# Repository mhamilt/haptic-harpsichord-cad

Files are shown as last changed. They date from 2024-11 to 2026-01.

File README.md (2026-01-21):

# Haptic Harpsichord CAD
Repository of CAD project files for the [Haptic Harpsichord](https://github.com/mhamilt/harpsichord-jack-tracking)

## Components

### QRE1113

- [QRE1113 Datasheet](https://www.mouser.in/datasheet/2/308/QRE1113-1121523.pdf)

|  |  |
| :---: | :---: |
| QRE1113 Dimension. Not that pin 1 should always have a chamfer on the corner to help identify it. | QRE1113 Pinout |

### Multiplexer

- Datasheet

### LEDs

- Datasheet

### Rotary

- Datasheet

### FRAM

- Datasheet

## Eagle 

### Automating EAGLE Commands

Below is python code used to generate commands that can be copy and pasted into EAGLE.

EAGLE has it's [ULP](https://web.mit.edu/xavid/arch/i386_rhel4/help/129.htm), but the intention here is to provide a light weight and easily modifiable system.

#### Faceboard

```py
qrepitch = 1.8 # placement is calculated from the #1 pin, pitch is used to offset to the centre
ox = 1.705     # min distance from board edge
oy = 1.705     # min distance from board edge in y axis
pitch = 14.02 # jack pitch
max_board_width = (6*pitch) + ox + qrepitch + ox

for index, point in enumerate([(x * pitch) + ox for x in range(0,7)]):
  print(f"move Q{index+1} ({oy} {point});")

resitor100k_ox = 10.1 # min distance from board edge in y axis
resitor100k_oy = 7.0 # min distance from board edge in y axis
resitor100_ox = 7.5 # min distance from board edge in y axis
resitor100_oy = 7.0 # min distance from board edge in y axis
rpitch = 12.9

for index, point in enumerate([(x * rpitch) + resitor100_oy for x in range(0,16)]):
  if index < 7:
    print(f"move R{(index*2)+1} ({resitor100_ox} {point});")
    print(f"move R{(index+1)*2} ({resitor10k_ox} {point});")
  if index >= 7:
    print(f"move R{((index+1)*2)+1} ({resitor100_ox} {point});")
    print(f"move R{((index+1)+1)*2} ({resitor10k_ox} {point});")

led_ox = 23.08 # min distance from board edge in x axis
led_ox = 23.68
# led_oy = 4.4 # min distance from board edge in y axis
# led_pitch = 12.0
led_pitch = 17.73 - 3.71
led_oy = 3.71 + (qrepitch/2) # min distance from board edge in y axis

for index, point in enumerate([(x * led_pitch) + led_oy for x in range(0,7)]):
  print(f"rotate D{(index+1)} 270;")
  print(f"move D{(7-index)} ({led_ox} {point});")
  print(f"mirror D{(index+1)};")

```

#### Sensor Board

```py
ox = 1.705         # mm min distance from board edge
oy = 1.705         # mm min distance from board edge in y axis
rotx = 3.55        # mm min x distance but for a 90 rotated sensor
jack_pitch = 14.02 # mm

led_ox = 23.08 # min distance from board edge in x axis
led_pitch = 17.73 - 3.71 # mini 3535 neopixels

for i, p in enumerate([(x * jack_pitch) + oy for x in range(0,7)]):
  print(f"ROTATE =R90 Q{i+1};")

for i, p in enumerate([(x * jack_pitch) + oy for x in range(0,7)]):
  print(f"move Q{i+1} ({rotx} {p});")

for i, p in enumerate([(x * led_pitch) + led_oy for x in range(0,7)]):
  print(f"ROTATE =R90 LED{i+1};")

for index, point in enumerate([(x * led_pitch) + led_oy for x in range(0,7)]):  
  print(f"move LED{(index+1)} ({led_ox} {point});")

for index, point in enumerate([(x * led_pitch) + led_oy for x in range(0,7)]):  
  print(f"mirror LED{(index+1)};")

```

#### Sensor Board SMD

```py
ox = 1.705         # mm min distance from board edge
oy = 1.705         # mm min distance from board edge in y axis
rotx = 3.55        # mm min x distance but for a 90 rotated sensor
jack_pitch = 14.02 # mm

led_ox = 23.08 # min distance from board edge in x axis
led_pitch = 17.73 - 3.71 # mini 3535 neopixels

for i, p in enumerate([(x * jack_pitch) + oy for x in range(0,7)]):
  print(f"ROTATE =R90 Q{i+1};")

for i, point in enumerate([(x * jack_pitch) + ox for x in range(0,7)]):
  print(f"move Q{i+1} ({oy} {p});")

for i, p in enumerate([(x * led_pitch) + led_oy for x in range(0,7)]):
  print(f"ROTATE =R90 LED{i+1};")

for i, p in enumerate([(x * led_pitch) + led_oy for x in range(0,7)]):  
  print(f"move LED{(i+1)} ({led_ox} {point});")

for i, p in enumerate([(x * led_pitch) + led_oy for x in range(0,7)]):  
  print(f"mirror LED{(i+1)};")

```

## Mount Holes

### Sensor Board

```
Mount Holes: (4.5 81.5), (4.5 11) 
```
### Signal Board

```
Mount Holes: (12.5 75), (12.5 18) 
```

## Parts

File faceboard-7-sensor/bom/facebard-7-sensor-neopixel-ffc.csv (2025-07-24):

Part | Value | Device | Package | Description | ARROW_PART_NUMBER | ARROW_PRICE-STOCK | COPYRIGHT | DESCRIPTION | HEIGHT | MANUFACTURER | MANUFACTURER_NAME | MANUFACTURER_PART_NUMBER | MAXIMUM_PACKAGE_HEIGHT | MFR_NAME | MOUSER_PART_NUMBER | MOUSER_PRICE-STOCK | PARTREV | POPULARITY | SPICEPREFIX | STANDARD
D1 | 1655 | 1655 | LED_1655 | Ws2812b 5050 Rgb Led With Integrated Driver Chip Pack Of 10 |  |  |  |  |  | Adafruit Industries |  |  | 1.6 mm |  |  |  | 01 |  |  | Manufacturer recommendations
D2 | 1655 | 1655 | LED_1655 | Ws2812b 5050 Rgb Led With Integrated Driver Chip Pack Of 10 |  |  |  |  |  | Adafruit Industries |  |  | 1.6 mm |  |  |  | 01 |  |  | Manufacturer recommendations
D3 | 1655 | 1655 | LED_1655 | Ws2812b 5050 Rgb Led With Integrated Driver Chip Pack Of 10 |  |  |  |  |  | Adafruit Industries |  |  | 1.6 mm |  |  |  | 01 |  |  | Manufacturer recommendations
D4 | 1655 | 1655 | LED_1655 | Ws2812b 5050 Rgb Led With Integrated Driver Chip Pack Of 10 |  |  |  |  |  | Adafruit Industries |  |  | 1.6 mm |  |  |  | 01 |  |  | Manufacturer recommendations
D5 | 1655 | 1655 | LED_1655 | Ws2812b 5050 Rgb Led With Integrated Driver Chip Pack Of 10 |  |  |  |  |  | Adafruit Industries |  |  | 1.6 mm |  |  |  | 01 |  |  | Manufacturer recommendations
D6 | 1655 | 1655 | LED_1655 | Ws2812b 5050 Rgb Led With Integrated Driver Chip Pack Of 10 |  |  |  |  |  | Adafruit Industries |  |  | 1.6 mm |  |  |  | 01 |  |  | Manufacturer recommendations
D7 | 1655 | 1655 | LED_1655 | Ws2812b 5050 Rgb Led With Integrated Driver Chip Pack Of 10 |  |  |  |  |  | Adafruit Industries |  |  | 1.6 mm |  |  |  | 01 |  |  | Manufacturer recommendations
FFCIN | 52806-1410 | 52806-1410 | 528061410 | Molex 2mm Pitch 14 Way Straight Female FPC Connector |  |  |  | Molex 2mm Pitch 14 Way Straight Female FPC Connector | 5.6mm |  | Molex | 52806-1410 |  |  | 538-52806-1410 | https://www.mouser.co.uk/ProductDetail/Molex/52806-1410?qs=%252BdbFUiYBkDYU5moeZz2crA%3D%3D
FFCOUT | 52806-1410 | 52806-1410 | 528061410 | Molex 2mm Pitch 14 Way Straight Female FPC Connector |  |  |  | Molex 2mm Pitch 14 Way Straight Female FPC Connector | 5.6mm |  | Molex | 52806-1410 |  |  | 538-52806-1410 | https://www.mouser.co.uk/ProductDetail/Molex/52806-1410?qs=%252BdbFUiYBkDYU5moeZz2crA%3D%3D
Q1 | QRE1113 | QRE1113 | DIP4_100AQ_ONS |  |  |  | Copyright (C) 2024 Ultra Librarian. All rights reserved. |  |  |  |  | QRE1113 |  | onsemi
Q2 | QRE1113 | QRE1113 | DIP4_100AQ_ONS |  |  |  | Copyright (C) 2024 Ultra Librarian. All rights reserved. |  |  |  |  | QRE1113 |  | onsemi
Q3 | QRE1113 | QRE1113 | DIP4_100AQ_ONS |  |  |  | Copyright (C) 2024 Ultra Librarian. All rights reserved. |  |  |  |  | QRE1113 |  | onsemi
Q4 | QRE1113 | QRE1113 | DIP4_100AQ_ONS |  |  |  | Copyright (C) 2024 Ultra Librarian. All rights reserved. |  |  |  |  | QRE1113 |  | onsemi
Q5 | QRE1113 | QRE1113 | DIP4_100AQ_ONS |  |  |  | Copyright (C) 2024 Ultra Librarian. All rights reserved. |  |  |  |  | QRE1113 |  | onsemi
Q6 | QRE1113 | QRE1113 | DIP4_100AQ_ONS |  |  |  | Copyright (C) 2024 Ultra Librarian. All rights reserved. |  |  |  |  | QRE1113 |  | onsemi
Q7 | QRE1113 | QRE1113 | DIP4_100AQ_ONS |  |  |  | Copyright (C) 2024 Ultra Librarian. All rights reserved. |  |  |  |  | QRE1113 |  | onsemi
R1 | 100 | R-EU_0207/10 | 0207/10 | RESISTOR, European symbol |  |  |  |  |  |  |  |  |  |  |  |  |  | 81 | R
R3 | 100 | R-EU_0207/10 | 0207/10 | RESISTOR, European symbol |  |  |  |  |  |  |  |  |  |  |  |  |  | 81 | R
R5 | 100 | R-EU_0207/10 | 0207/10 | RESISTOR, European symbol |  |  |  |  |  |  |  |  |  |  |  |  |  | 81 | R
R7 | 100 | R-EU_0207/10 | 0207/10 | RESISTOR, European symbol |  |  |  |  |  |  |  |  |  |  |  |  |  | 81 | R
R9 | 100 | R-EU_0207/10 | 0207/10 | RESISTOR, European symbol |  |  |  |  |  |  |  |  |  |  |  |  |  | 81 | R
R11 | 100 | R-EU_0207/10 | 0207/10 | RESISTOR, European symbol |  |  |  |  |  |  |  |  |  |  |  |  |  | 81 | R
R13 | 100 | R-EU_0207/10 | 0207/10 | RESISTOR, European symbol |  |  |  |  |  |  |  |  |  |  |  |  |  | 81 | R
RDV | 100k | R-EU_0207/10 | 0207/10 | RESISTOR, European symbol |  |  |  |  |  |  |  |  |  |  |  |  |  | 81 | R
SJ1 |  | SJ | SJ | SMD solder JUMPER |  |  |  |  |  |  |  |  |  |  |  |  |  | 33
SJ2 |  | SJ | SJ | SMD solder JUMPER |  |  |  |  |  |  |  |  |  |  |  |  |  | 33
SJ3 |  | SJ | SJ | SMD solder JUMPER |  |  |  |  |  |  |  |  |  |  |  |  |  | 33
SJ4 |  | SJ | SJ | SMD solder JUMPER |  |  |  |  |  |  |  |  |  |  |  |  |  | 33
SJ5 |  | SJ | SJ | SMD solder JUMPER |  |  |  |  |  |  |  |  |  |  |  |  |  | 33
SJ6 |  | SJ | SJ | SMD solder JUMPER |  |  |  |  |  |  |  |  |  |  |  |  |  | 33
SJ7 |  | SJ | SJ | SMD solder JUMPER |  |  |  |  |  |  |  |  |  |  |  |  |  | 33
U1 | CD4051BE | CD4051BE | N16 |  |  |  | Copyright (C) 2024 Ultra Librarian. All rights reserved. |  |  |  |  | CD4051BE |  | Texas Instruments

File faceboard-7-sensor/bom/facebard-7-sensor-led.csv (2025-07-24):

Part | Value | Device | Package | Description | COPYRIGHT | MANUFACTURER | MANUFACTURER_PART_NUMBER | MAXIMUM_PACKAGE_HEIGHT | MF | MFR_NAME | MPN | OC_FARNELL | OC_NEWARK | PARTREV | POPULARITY | SPICEPREFIX | STANDARD
D1 | 1655 | 1655 | LED_1655 | Ws2812b 5050 Rgb Led With Integrated Driver Chip Pack Of 10 |  | Adafruit Industries |  | 1.6 mm |  |  |  |  |  | 01 |  |  | Manufacturer recommendations
D2 | 1655 | 1655 | LED_1655 | Ws2812b 5050 Rgb Led With Integrated Driver Chip Pack Of 10 |  | Adafruit Industries |  | 1.6 mm |  |  |  |  |  | 01 |  |  | Manufacturer recommendations
D3 | 1655 | 1655 | LED_1655 | Ws2812b 5050 Rgb Led With Integrated Driver Chip Pack Of 10 |  | Adafruit Industries |  | 1.6 mm |  |  |  |  |  | 01 |  |  | Manufacturer recommendations
D4 | 1655 | 1655 | LED_1655 | Ws2812b 5050 Rgb Led With Integrated Driver Chip Pack Of 10 |  | Adafruit Industries |  | 1.6 mm |  |  |  |  |  | 01 |  |  | Manufacturer recommendations
D5 | 1655 | 1655 | LED_1655 | Ws2812b 5050 Rgb Led With Integrated Driver Chip Pack Of 10 |  | Adafruit Industries |  | 1.6 mm |  |  |  |  |  | 01 |  |  | Manufacturer recommendations
D6 | 1655 | 1655 | LED_1655 | Ws2812b 5050 Rgb Led With Integrated Driver Chip Pack Of 10 |  | Adafruit Industries |  | 1.6 mm |  |  |  |  |  | 01 |  |  | Manufacturer recommendations
D7 | 1655 | 1655 | LED_1655 | Ws2812b 5050 Rgb Led With Integrated Driver Chip Pack Of 10 |  | Adafruit Industries |  | 1.6 mm |  |  |  |  |  | 01 |  |  | Manufacturer recommendations
Q1 | QRE1113 | QRE1113 | DIP4_100AQ_ONS |  | Copyright (C) 2024 Ultra Librarian. All rights reserved. |  | QRE1113 |  |  | onsemi
Q2 | QRE1113 | QRE1113 | DIP4_100AQ_ONS |  | Copyright (C) 2024 Ultra Librarian. All rights reserved. |  | QRE1113 |  |  | onsemi
Q3 | QRE1113 | QRE1113 | DIP4_100AQ_ONS |  | Copyright (C) 2024 Ultra Librarian. All rights reserved. |  | QRE1113 |  |  | onsemi
Q4 | QRE1113 | QRE1113 | DIP4_100AQ_ONS |  | Copyright (C) 2024 Ultra Librarian. All rights reserved. |  | QRE1113 |  |  | onsemi
Q5 | QRE1113 | QRE1113 | DIP4_100AQ_ONS |  | Copyright (C) 2024 Ultra Librarian. All rights reserved. |  | QRE1113 |  |  | onsemi
Q6 | QRE1113 | QRE1113 | DIP4_100AQ_ONS |  | Copyright (C) 2024 Ultra Librarian. All rights reserved. |  | QRE1113 |  |  | onsemi
Q7 | QRE1113 | QRE1113 | DIP4_100AQ_ONS |  | Copyright (C) 2024 Ultra Librarian. All rights reserved. |  | QRE1113 |  |  | onsemi
R1 | 100 | R-EU_0207/10 | 0207/10 | RESISTOR, European symbol |  |  |  |  |  |  |  |  |  |  | 81 | R
R2 | 100k | R-EU_0207/10 | 0207/10 | RESISTOR, European symbol |  |  |  |  |  |  |  |  |  |  | 81 | R
R3 | 100 | R-EU_0207/10 | 0207/10 | RESISTOR, European symbol |  |  |  |  |  |  |  |  |  |  | 81 | R
R4 | 100k | R-EU_0207/10 | 0207/10 | RESISTOR, European symbol |  |  |  |  |  |  |  |  |  |  | 81 | R
R5 | 100 | R-EU_0207/10 | 0207/10 | RESISTOR, European symbol |  |  |  |  |  |  |  |  |  |  | 81 | R
R6 | 100k | R-EU_0207/10 | 0207/10 | RESISTOR, European symbol |  |  |  |  |  |  |  |  |  |  | 81 | R
R7 | 100 | R-EU_0207/10 | 0207/10 | RESISTOR, European symbol |  |  |  |  |  |  |  |  |  |  | 81 | R
R8 | 100k | R-EU_0207/10 | 0207/10 | RESISTOR, European symbol |  |  |  |  |  |  |  |  |  |  | 81 | R
R9 | 100 | R-EU_0207/10 | 0207/10 | RESISTOR, European symbol |  |  |  |  |  |  |  |  |  |  | 81 | R
R10 | 10k | R-EU_0207/10 | 0207/10 | RESISTOR, European symbol |  |  |  |  |  |  |  |  |  |  | 81 | R
R11 | 100 | R-EU_0207/10 | 0207/10 | RESISTOR, European symbol |  |  |  |  |  |  |  |  |  |  | 81 | R
R12 | 100k | R-EU_0207/10 | 0207/10 | RESISTOR, European symbol |  |  |  |  |  |  |  |  |  |  | 81 | R
R13 | 100 | R-EU_0207/10 | 0207/10 | RESISTOR, European symbol |  |  |  |  |  |  |  |  |  |  | 81 | R
R14 | 100k | R-EU_0207/10 | 0207/10 | RESISTOR, European symbol |  |  |  |  |  |  |  |  |  |  | 81 | R
SV2 | header | MA08-1 | MA08-1 | PIN HEADER |  |  |  |  |  |  |  | unknown | unknown |  | 10 | X
SV3 | header | MA08-1 | MA08-1 | PIN HEADER |  |  |  |  |  |  |  | unknown | unknown |  | 10
U1 | CD4051BE | CD4051BE | N16 |  | Copyright (C) 2024 Ultra Librarian. All rights reserved. |  | CD4051BE |  |  | Texas Instruments

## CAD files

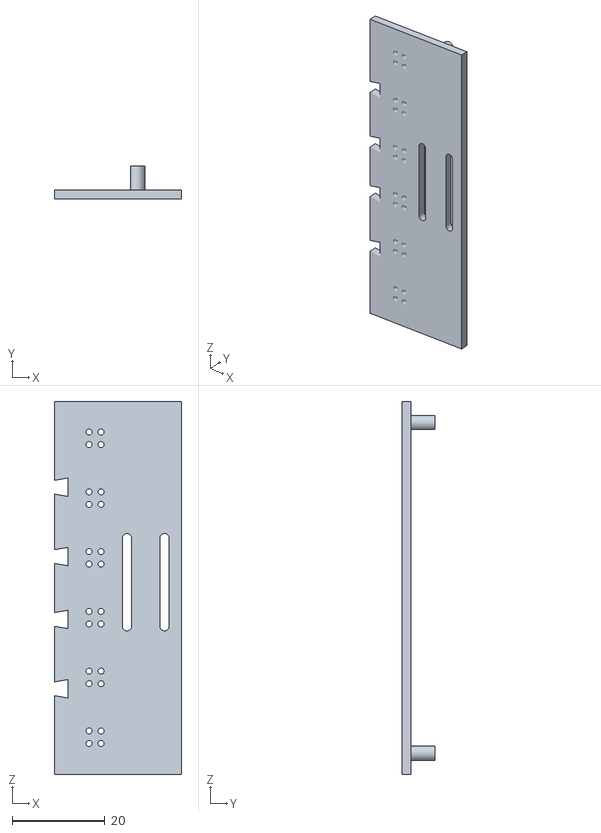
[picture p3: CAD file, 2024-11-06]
faceboard-7-sensor/stl/bracket.stl
27.5 x 7.20 x 80.5

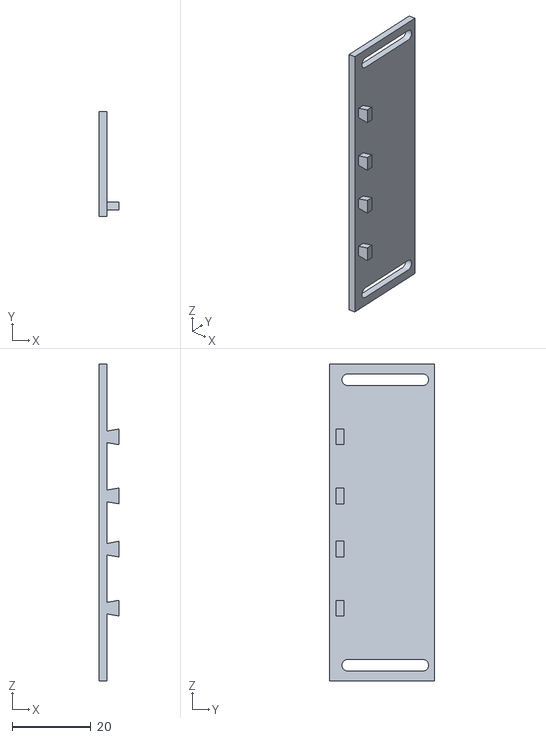
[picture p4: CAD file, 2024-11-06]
faceboard-7-sensor/stl/adjuster.stl
5.00 x 26.7 x 80.5

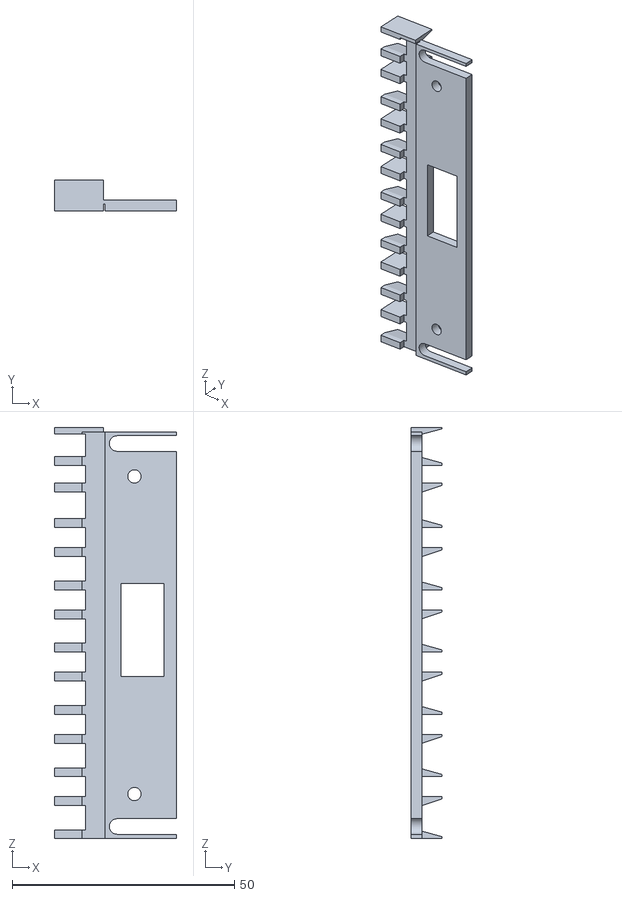
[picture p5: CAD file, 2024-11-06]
faceboard-7-sensor/stl/baffles.stl
27.5 x 7.00 x 92.4

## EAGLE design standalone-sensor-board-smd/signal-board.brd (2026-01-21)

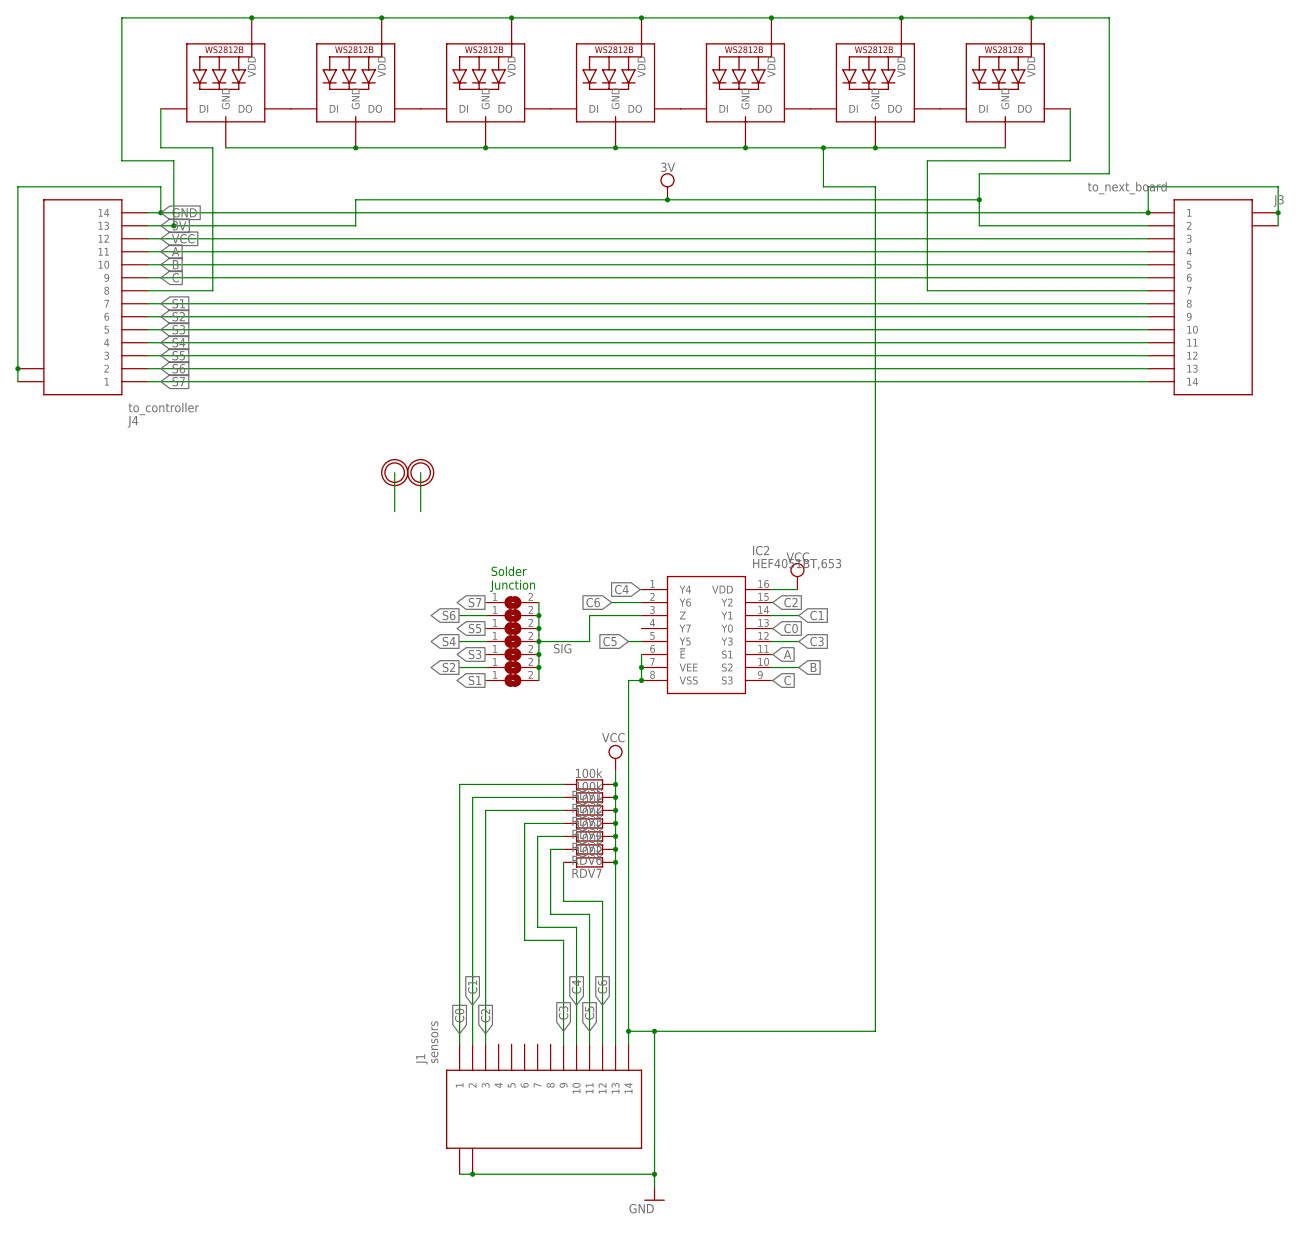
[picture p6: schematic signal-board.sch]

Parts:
IC2: HEF4051BT,653; HEF4051BT653
J1: sensors; 686114148922
J3: to_next_board; 686114148922
J4: to_controller; 686114148922
LED1, LED2, LED3, LED4, LED5, LED6, LED7: WS2812B3535; LED3535
RDV1, RDV2, RDV3, RDV4, RDV5, RDV6, RDV7: 100k; R0805
SJ1, SJ2, SJ3, SJ4, SJ5, SJ6, SJ7: SJ
U$1, U$2: MICROBUILDER_MOUNTINGHOLEMICROBUILDER_MOUNTINGHOL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; MICROBUILDER_MOUNTINGHOLE_4.0_PLATEDTHIN

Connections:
3V: J3.2, J4.13, LED1.2 (VDD), LED2.2 (VDD), LED3.2 (VDD), LED4.2 (VDD), LED5.2 (VDD), LED6.2 (VDD), LED7.2 (VDD)
A: IC2.11 (S1), J3.4, J4.11
B: IC2.10 (S2), J3.5, J4.10
C: IC2.9 (S3), J3.6, J4.9
C0: IC2.13 (Y0), J1.1, RDV1.2
C1: IC2.14 (Y1), J1.2, RDV2.2
C2: IC2.15 (Y2), J1.3, RDV3.2
C3: IC2.12 (Y3), J1.9, RDV4.2
C4: IC2.1 (Y4), J1.10, RDV5.2
C5: IC2.5 (Y5), J1.11, RDV6.2
C6: IC2.2 (Y6), J1.12, RDV7.2
DIN: J4.8, LED1.1 (DI)
DOUT: J3.7, LED7.3 (DO)
GND: IC2.6 (!E), IC2.7 (VEE), IC2.8 (VSS), J1.14, J1.MP1, J1.MP2, J3.1, J3.MP1, J3.MP2, J4.14, J4.MP1, J4.MP2, LED1.4 (GND), LED2.4 (GND), LED3.4 (GND), LED4.4 (GND), LED5.4 (GND), LED6.4 (GND), LED7.4 (GND)
unnamed: LED1.3 (DO), LED2.1 (DI)
unnamed: LED2.3 (DO), LED3.1 (DI)
unnamed: LED3.3 (DO), LED4.1 (DI)
unnamed: LED4.3 (DO), LED5.1 (DI)
unnamed: LED5.3 (DO), LED6.1 (DI)
unnamed: LED6.3 (DO), LED7.1 (DI)
S1: J3.8, J4.7, SJ1.1
S2: J3.9, J4.6, SJ2.1
S3: J3.10, J4.5, SJ3.1
S4: J3.11, J4.4, SJ4.1
S5: J3.12, J4.3, SJ5.1
S6: J3.13, J4.2, SJ6.1
S7: J3.14, J4.1, SJ7.1
SIG: IC2.3 (Z), SJ1.2, SJ2.2, SJ3.2, SJ4.2, SJ5.2, SJ6.2, SJ7.2
VCC: IC2.16 (VDD), J1.13, J3.3, J4.12, RDV1.1, RDV2.1, RDV3.1, RDV4.1, RDV5.1, RDV6.1, RDV7.1

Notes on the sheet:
Solder Junction

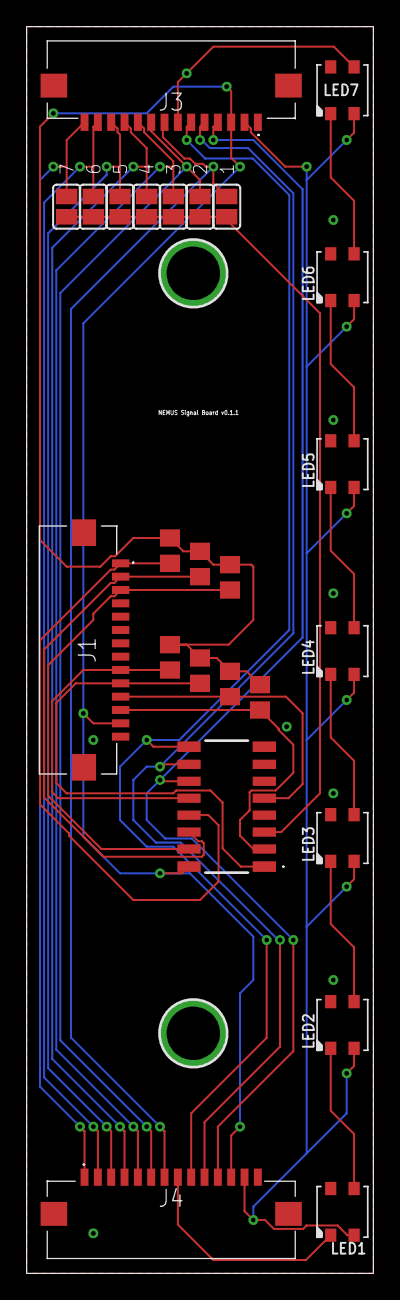
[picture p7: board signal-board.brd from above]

Board: 2 copper layers, 26.0 x 93.5 mm, 27 parts (0 on the bottom side), 29 nets.

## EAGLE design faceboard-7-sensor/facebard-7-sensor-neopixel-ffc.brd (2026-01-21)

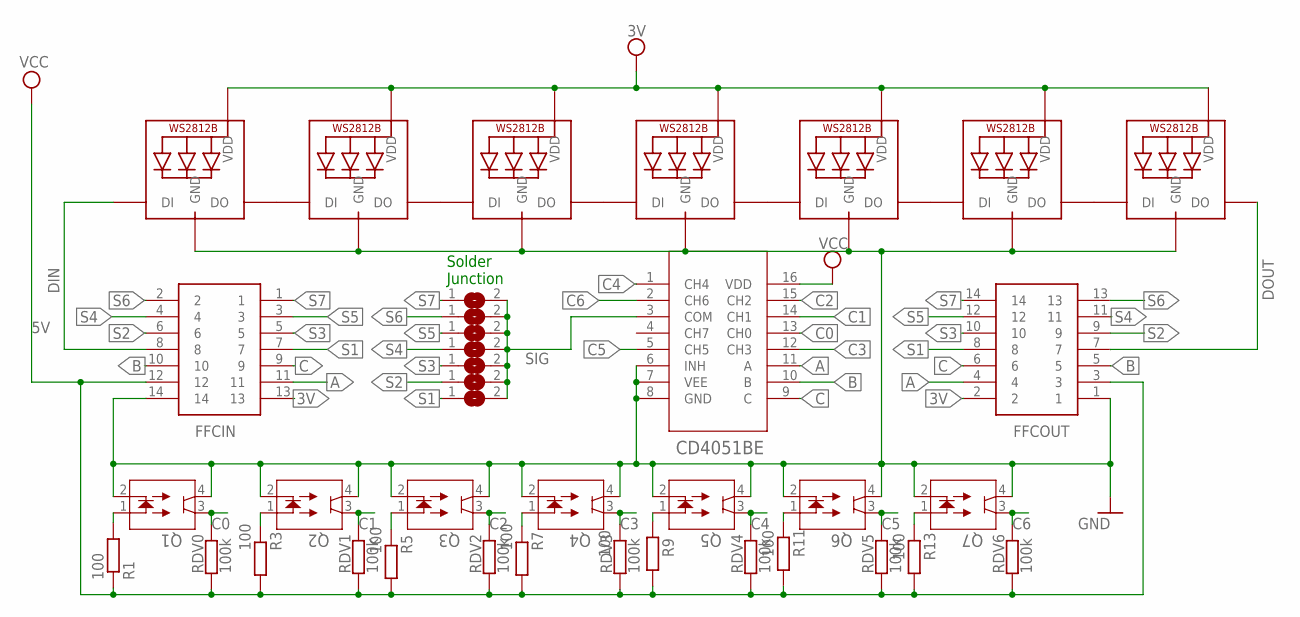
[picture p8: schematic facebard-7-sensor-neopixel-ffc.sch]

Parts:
FFCIN: 52806-1410; 528061410
FFCOUT: 52806-1410; 528061410
LED1, LED2, LED3, LED4, LED5, LED6, LED7: WS2812B3535; LED3535
Q1, Q2, Q3, Q4, Q5, Q6, Q7: QRE1113; DIP4_100AQ_ONS
R1, R3, R5, R7, R9, R11, R13: 100; 0207/10
RDV0, RDV1, RDV2, RDV3, RDV4, RDV5, RDV6: 100k; 0207/10
SJ1, SJ2, SJ3, SJ4, SJ5, SJ6, SJ7: SJ
U1: CD4051BE; N16

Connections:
3V: FFCIN.13, FFCOUT.2, LED1.2 (VDD), LED2.2 (VDD), LED3.2 (VDD), LED4.2 (VDD), LED5.2 (VDD), LED6.2 (VDD), LED7.2 (VDD)
5V: FFCIN.12, FFCOUT.3, R1.1, R3.1, R5.1, R7.1, R9.1, R11.1, R13.1, RDV0.1, RDV1.1, RDV2.1, RDV3.1, RDV4.1, RDV5.1, RDV6.1, U1.16 (VDD)
A: FFCIN.11, FFCOUT.4, U1.11 (A)
B: FFCIN.10, FFCOUT.5, U1.10 (B)
C: FFCIN.9, FFCOUT.6, U1.9 (C)
C0: Q1.3, RDV0.2, U1.13 (CH0)
C1: Q2.3, RDV1.2, U1.14 (CH1)
C2: Q3.3, RDV2.2, U1.15 (CH2)
C3: Q4.3, RDV3.2, U1.12 (CH3)
C4: Q5.3, RDV4.2, U1.1 (CH4)
C5: Q6.3, RDV5.2, U1.5 (CH5)
C6: Q7.3, RDV6.2, U1.2 (CH6)
DIN: FFCIN.8, LED1.1 (DI)
DOUT: FFCOUT.7, LED7.3 (DO)
GND: FFCIN.14, FFCOUT.1, LED1.4 (GND), LED2.4 (GND), LED3.4 (GND), LED4.4 (GND), LED5.4 (GND), LED6.4 (GND), LED7.4 (GND), Q1.2, Q1.4, Q2.2, Q2.4, Q3.2, Q3.4, Q4.2, Q4.4, Q5.2, Q5.4, Q6.2, Q6.4, Q7.2, Q7.4, U1.6 (INH), U1.7 (VEE), U1.8 (GND)
unnamed: Q1.1, R1.2
unnamed: Q2.1, R3.2
unnamed: LED1.3 (DO), LED2.1 (DI)
unnamed: Q3.1, R5.2
unnamed: LED2.3 (DO), LED3.1 (DI)
unnamed: Q4.1, R7.2
unnamed: LED3.3 (DO), LED4.1 (DI)
unnamed: LED4.3 (DO), LED5.1 (DI)
unnamed: LED5.3 (DO), LED6.1 (DI)
unnamed: Q6.1, R11.2
unnamed: LED6.3 (DO), LED7.1 (DI)
unnamed: Q7.1, R13.2
unnamed: Q5.1, R9.2
S1: FFCIN.7, FFCOUT.8, SJ1.1
S2: FFCIN.6, FFCOUT.9, SJ2.1
S3: FFCIN.5, FFCOUT.10, SJ3.1
S4: FFCIN.4, FFCOUT.11, SJ4.1
S5: FFCIN.3, FFCOUT.12, SJ5.1
S6: FFCIN.2, FFCOUT.13, SJ6.1
S7: FFCIN.1, FFCOUT.14, SJ7.1
SIG: SJ1.2, SJ2.2, SJ3.2, SJ4.2, SJ5.2, SJ6.2, SJ7.2, U1.3 (COM)

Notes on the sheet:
Solder Junction

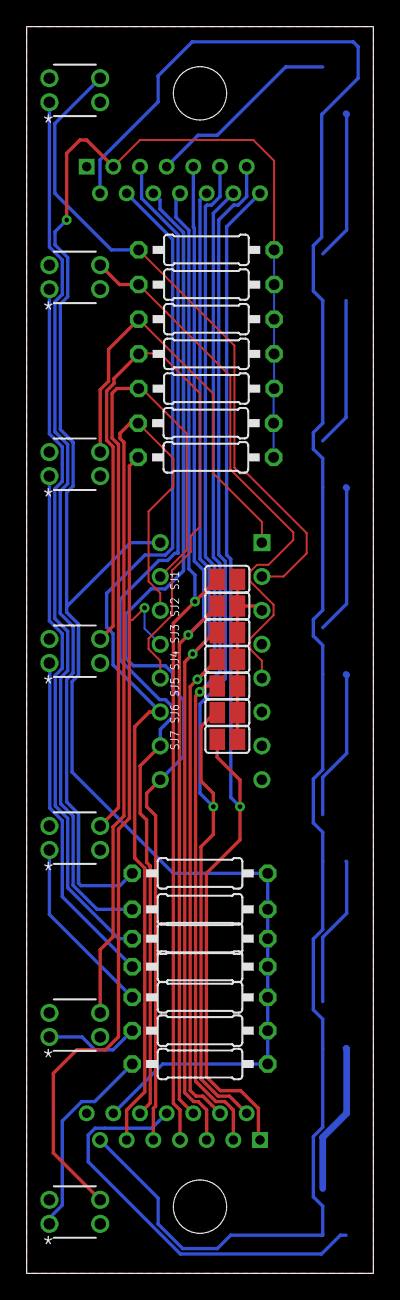
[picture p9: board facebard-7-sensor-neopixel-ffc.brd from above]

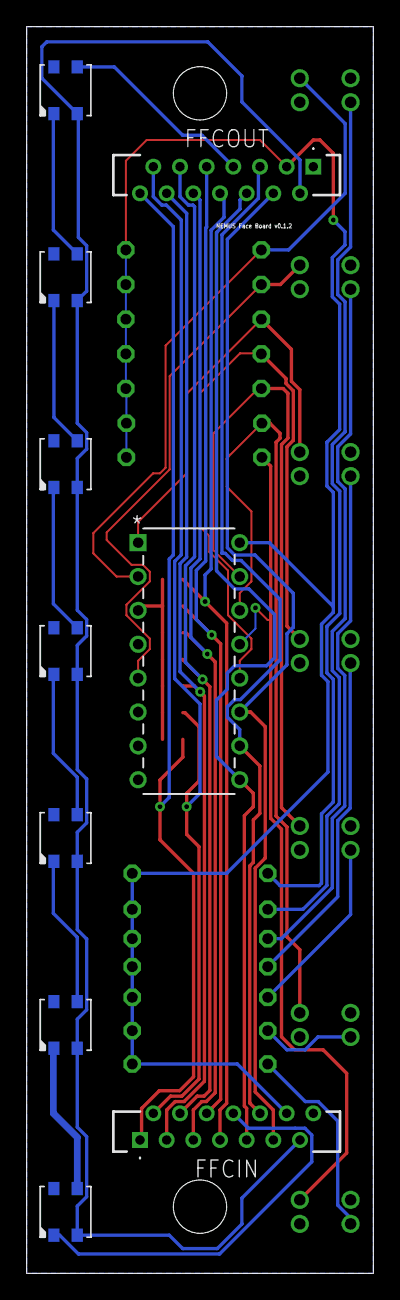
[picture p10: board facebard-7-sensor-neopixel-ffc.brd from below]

Board: 2 copper layers, 26.0 x 93.5 mm, 38 parts (10 on the bottom side), 36 nets.

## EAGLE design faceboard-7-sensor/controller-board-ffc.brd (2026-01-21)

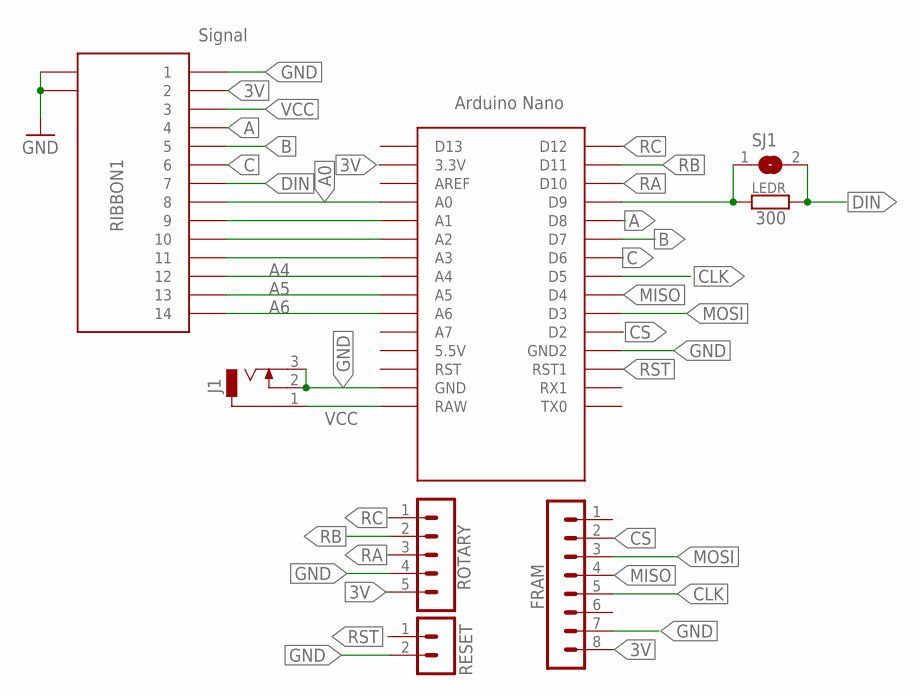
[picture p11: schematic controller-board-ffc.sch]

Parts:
FRAM: MB85RS2MTA; MA08-1
J1: DCJ0202
LEDR: 300; 0207/10
RESET: B2B-PH-K
RIBBON1: Signal; 686114148922
ROTARY: B5B-PH-K
SJ1: SJ
U$1: NANO

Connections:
3V: FRAM.8, RIBBON1.2, ROTARY.5, U$1.3.3V
A: RIBBON1.4, U$1.D8
A0: RIBBON1.8, U$1.A0
A1: RIBBON1.9, U$1.A1
A2: RIBBON1.10, U$1.A2
A3: RIBBON1.11, U$1.A3
A4: RIBBON1.12, U$1.A4
A5: RIBBON1.13, U$1.A5
A6: RIBBON1.14, U$1.A6
B: RIBBON1.5, U$1.D7
C: RIBBON1.6, U$1.D6
CLK: FRAM.5, U$1.D5
CS: FRAM.2, U$1.D2
D9: LEDR.1, SJ1.1, U$1.D9
DIN: LEDR.2, RIBBON1.7, SJ1.2
GND: FRAM.7, J1.2, J1.3, RESET.2, RIBBON1.1, RIBBON1.MP1, RIBBON1.MP2, ROTARY.4, U$1.GND, U$1.GND1 (GND2)
MISO: FRAM.4, U$1.D4
MOSI: FRAM.3, U$1.D3
RA: ROTARY.3, U$1.D10
RB: ROTARY.2, U$1.D11
RC: ROTARY.1, U$1.D12
RST: RESET.1, U$1.RST1
VCC: J1.1, RIBBON1.3, U$1.RAW

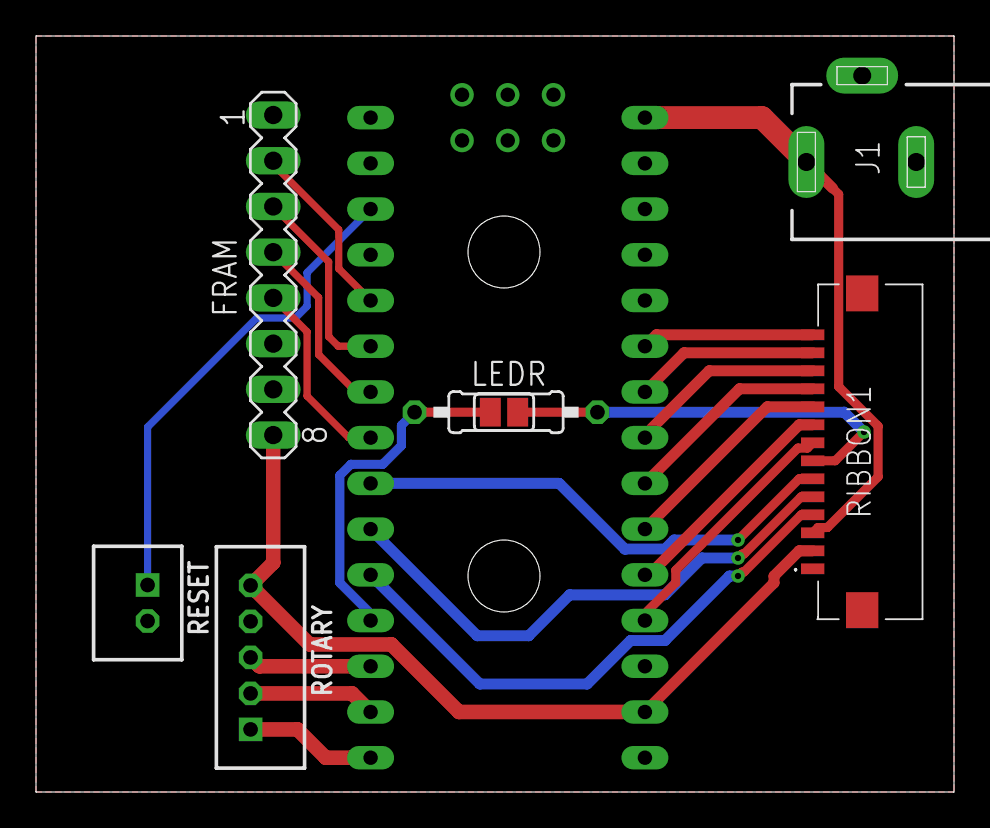
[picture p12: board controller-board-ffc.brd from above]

Board: 2 copper layers, 51.0 x 42.0 mm, 8 parts (0 on the bottom side), 23 nets.

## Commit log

2024-11-06 add original LED board
    [facebard-7-sensor-led.brd, facebard-7-sensor-led.sch, facebard-7-sensor-neopixel-ffc.brd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]
2024-11-06 add bracket `.stl` files
    [Bracket.stl, adjuster.stl, baffles.stl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]
2024-11-11 add ffc
    [controller-board-ffc.brd, controller-board-ffc.sch, facebard-7-sensor-neopixel-ffc.brd]
2024-11-11 remove 0.5mm ffc
    [facebard-7-sensor-neopixel-ffc.brd, facebard-7-sensor-neopixel-ffc.sch]
2024-11-21 add ffc boards
    [controller-board-ffc.brd, controller-board-ffc.sch, controller-board.brd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]
2025-01-07 tidy labelling
    [controller-board.brd, facebard-7-sensor-led.brd]
2025-07-24 add bom
    [facebard-7-sensor-led.csv]
2025-07-24 tidy routing
    [controller-board-ffc.brd, controller-board-ffc.sch]
2025-07-24 update divide resistor value
    [facebard-7-sensor-neopixel-ffc.csv]
2025-07-24 change divide resistor value
    [facebard-7-sensor-neopixel-ffc.brd, facebard-7-sensor-neopixel-ffc.sch]
2025-07-24 tidy connections
    [controller-board-ffc.sch]
2025-08-26 re-draw schematics
    [double-wired-3-face-board.brd, double-wired-3-face-board.sch, facebard-7-sensor-led.brd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]
2025-08-26 fix vcc net
    [facebard-7-sensor-led.brd, facebard-7-sensor-led.sch]
2025-08-26 add din dout labels
    [facebard-7-sensor-led.brd, facebard-7-sensor-led.sch]
2025-08-26 add sig label
    [facebard-7-sensor-neopixel-ffc.sch]
2025-08-26 redraw schematics
    [controller-board-ffc.brd, controller-board-ffc.sch, controller-board.brd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]
2025-12-12 add miniboard
    [miniboard-schem.brd, miniboard-schem.sch]
2025-12-12 init standalone design
    [controller-board.brd, controller-board.sch, sensor-board.brd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]
2025-12-12 sensor board
    [sensor-board.brd, sensor-board.sch]
2025-12-12 init smd version
    [controller-board.brd, controller-board.sch, sensor-board.brd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]
2025-12-12 rough layout
    [signal-board.brd, signal-board.sch]
2025-12-12 init smd
    [sensor-board.brd, sensor-board.sch]
2026-01-17 rewire mini leds and dividing resistors
    [facebard-7-sensor-neopixel-ffc.brd, facebard-7-sensor-neopixel-ffc.sch]
2026-01-17 fix signal routing
    [facebard-7-sensor-neopixel-ffc.brd, facebard-7-sensor-neopixel-ffc.sch]
2026-01-17 add smd board
    [facebard-7-sensor-smd.brd, facebard-7-sensor-smd.sch]
2026-01-17 add divider resistors
    [signal-board.brd, signal-board.sch]
2026-01-20 set rdvs
    [signal-board.brd, signal-board.sch]
2026-01-20 add smd boards from standalone
    [controller-board.brd, sensor-board.brd, sensor-board.sch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]
2026-01-20 sensor board routing
    [sensor-board.brd]
2026-01-20 signal board routing
    [signal-board.brd, signal-board.sch]
2026-01-20 add mounting holes
    [signal-board.brd, signal-board.sch]
2026-01-21 clear out old boards
    [Bracket.stl, adjuster.stl, controller-board.brd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]
2026-01-21 tidy silk screen
    [controller-board-ffc.brd, controller-board-ffc.sch, facebard-7-sensor-neopixel-ffc.brd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]
2026-01-21 set GND
    [signal-board.sch]
2026-01-21 add version labels
    [sensor-board.brd]
2026-01-21 fix version number
    [facebard-7-sensor-neopixel-ffc.brd]
2026-01-21 tidy layers
    [signal-board.brd]

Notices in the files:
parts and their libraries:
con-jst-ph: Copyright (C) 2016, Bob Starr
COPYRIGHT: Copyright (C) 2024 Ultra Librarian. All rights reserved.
